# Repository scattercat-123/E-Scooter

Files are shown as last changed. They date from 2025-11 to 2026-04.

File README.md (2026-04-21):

# E-Scooter
## The powerfull electronic scooter with suspension and a 1 hour battery.

## Why its special:
 - has a powerfull motor using a chain link system better than wheel hub system found in mordern scooters.
 - A high capacity battery for extended uses
 - Digital system with throttle, brakes and Battery managment system
 - has a really good custom front wheel suspension.

## Why did I make this?
Hardware projects are fun to make and i wanted something more fun than walking while travelling from one place to another.

## How does it work?
this electric scooter works by using a 24v batte ry pack made from 18650 cells arranged in a 7s 4p configuration which provides the required voltage and enough current to run the scooter. the battery is managed by a bms which protects it from overcharge and overdischarge and balances the cells so the pack stays healthy and also lets it charge . power from the battery goes into the motor controller which regulates how much current flows to the my1020 500W motor depending on throttle input. the motor converts this electrical energy into rotational motion by drivingg the chain which spins the rear wheel and makes it move. the headset and frame hold everything aligned so the power transfer is efficient. the suspension is custom built with 2 cycle supensions attached on a 2 part linkage system, the suspension has enough clearance so that the scooter can easily travel over any bumps and terrain on the way.

## pics









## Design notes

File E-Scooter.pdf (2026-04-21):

# E-Scooter

## Assembly

Github: https://github.com/scattercat-123/E-Scooter

## Cut Mild Steel Sheets, Pipes & Tubes for Frame (x7)

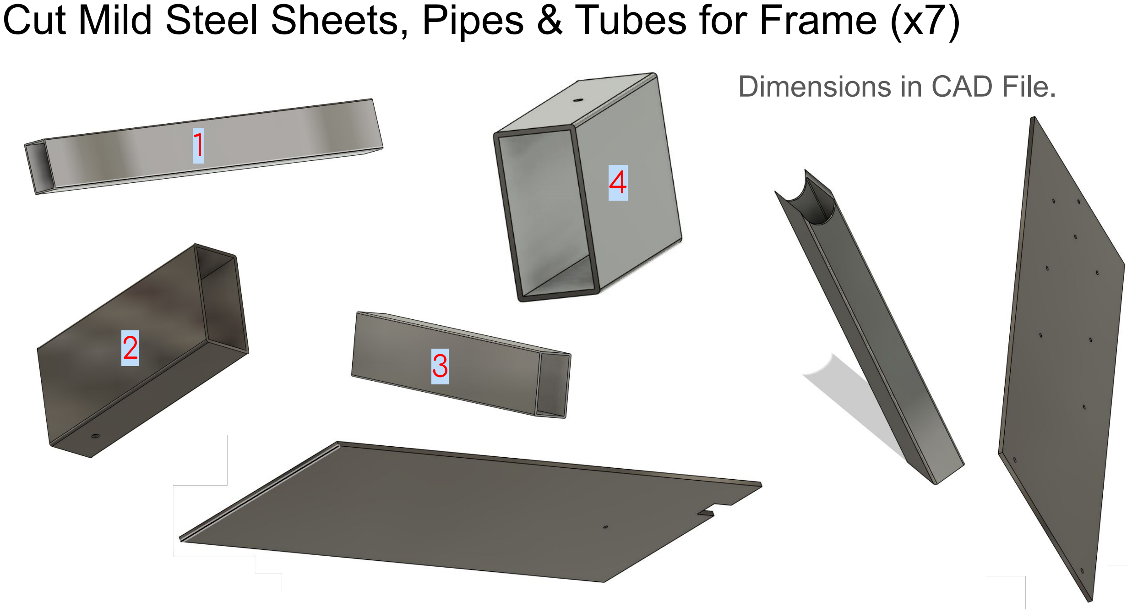
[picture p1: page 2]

Dimensions in CAD File.
1

2
3

4

## Step 1: Basic frame shape

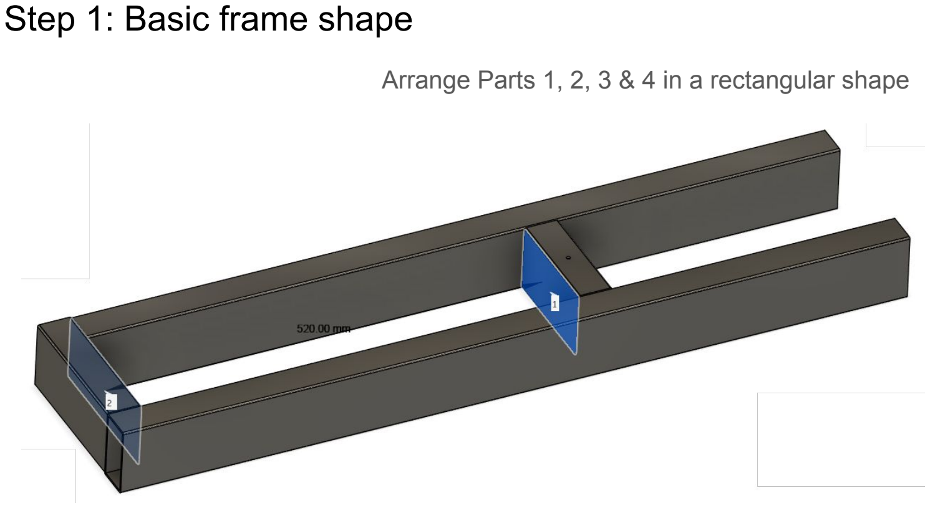
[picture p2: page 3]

Arrange Parts 1, 2, 3 & 4 in a rectangular shape

## Step 2: Basic frame shape

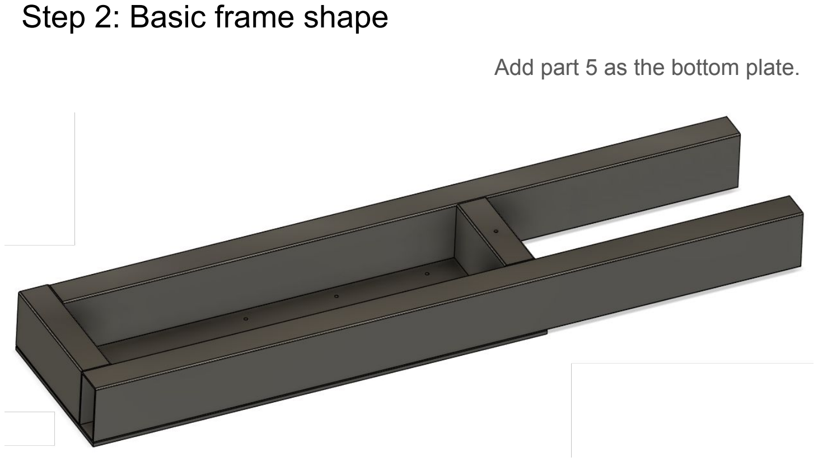
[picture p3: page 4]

Add part 5 as the bottom plate.

## Step 1: Electronics

Make the battery pack with 7S4P configuration by spot welding and adding spacers

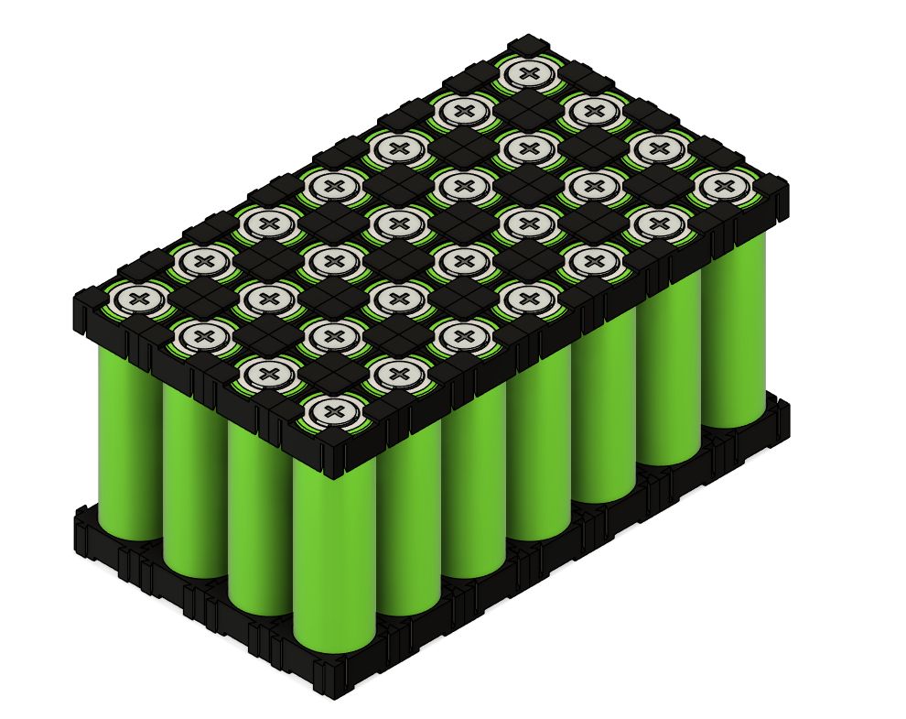
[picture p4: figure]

Watch this video to for an example about spot welding parallel and series cells for custom packs: https://www.youtube.com/watch?v=RuA0cUinqzA (https://www.youtube.com/watch?v=RuA0cUinqzA)

Note: Make sure to use 7S4P or even 5P configuration only!!

## Step 2: Electronics

Attach the BMS to the battery pack and wire according to the datasheet

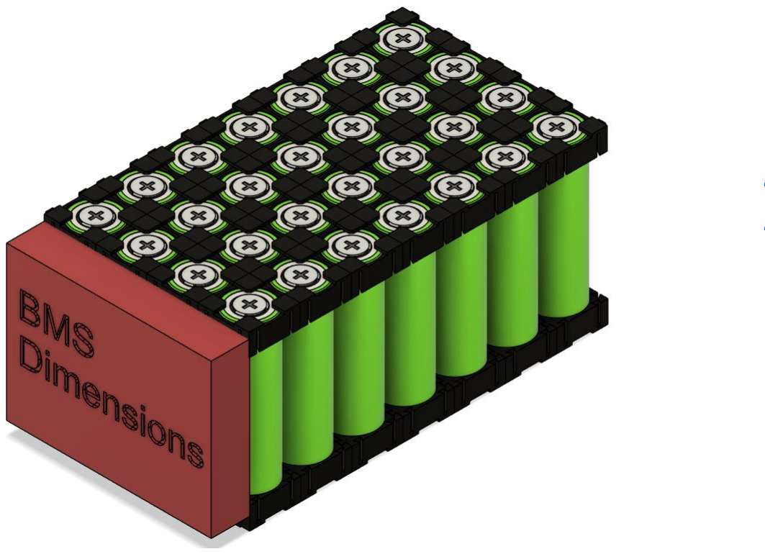
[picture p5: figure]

Here is a video by the bms manufacturer on how to wire the battery pack:
https://www.youtube.com/watch?v=KX7jc_Q_Cb8 (https://www.youtube.com/watch?v=KX7jc_Q_Cb8)

## Step 3: Basic frame shape

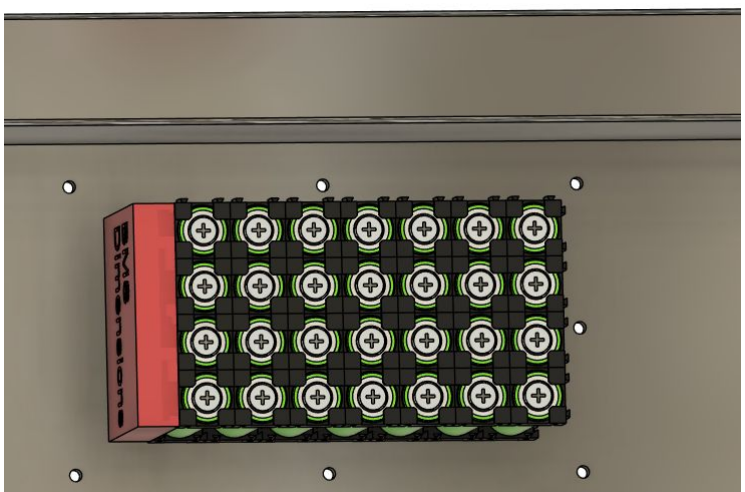
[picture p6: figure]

Place the battery inside the box made by the screw holes

## Step 4: Basic frame shape

Screw on the 3d printed battery cover and make sure no water/dust can enter

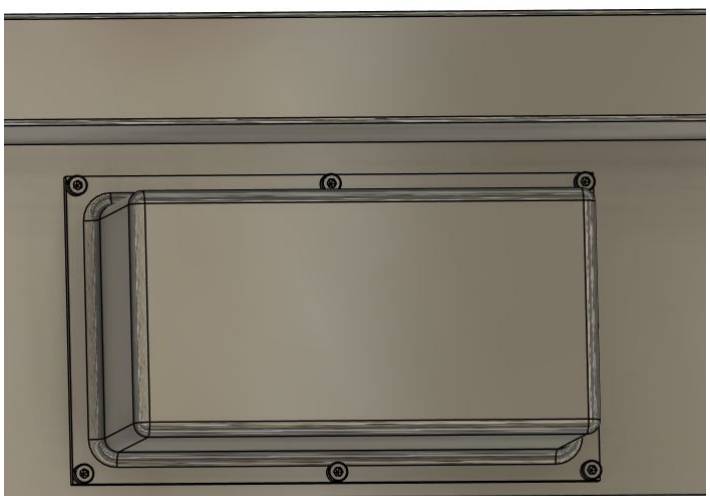
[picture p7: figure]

## Step 5: Basic frame shape

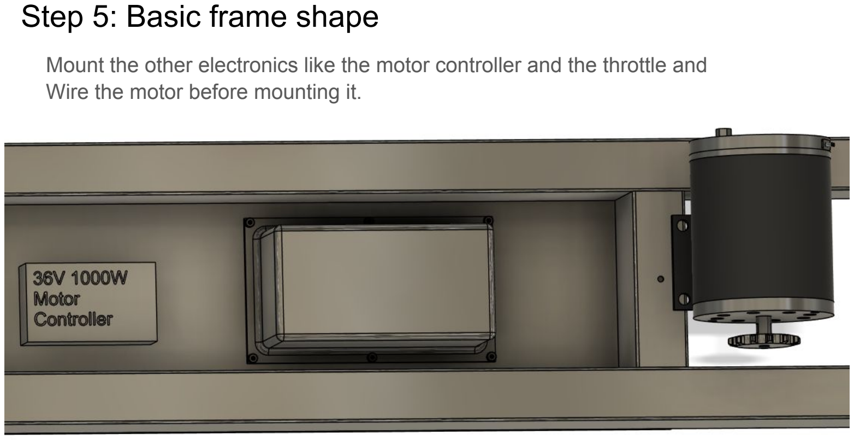
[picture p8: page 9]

Mount the other electronics like the motor controller and the throttle and Wire the motor before mounting it.

## Step 5: Basic frame shape

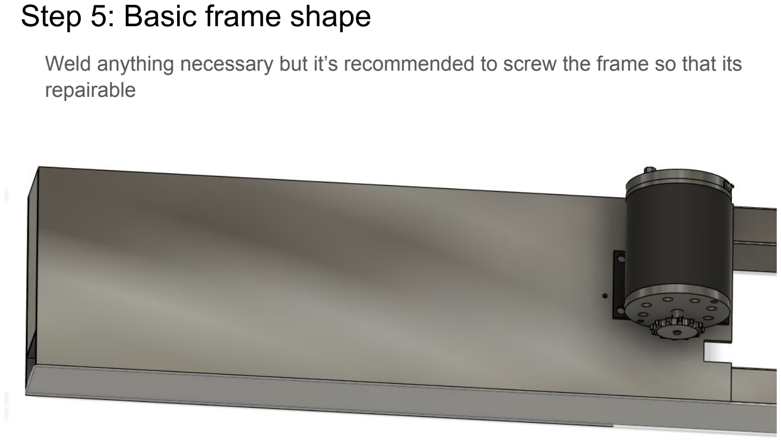
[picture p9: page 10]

Weld anything necessary but it’s recommended to screw the frame so that its repairable

## Step 1: Handlebars

Weld the handle support

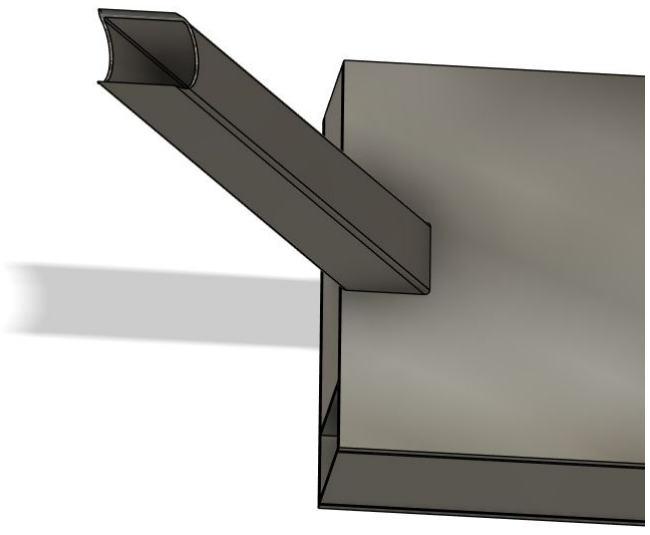
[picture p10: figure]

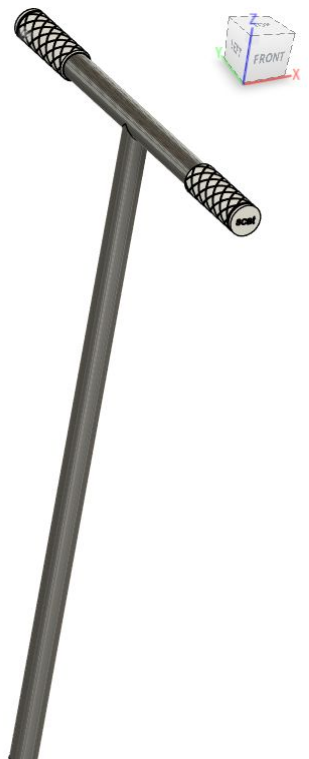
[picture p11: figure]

## Step 1: Handlebars

Make the T Handlebar shape

Obviously the white handlebars are just for a model but make sure to put the correct electronic ones with a throttle and perhaps a display?

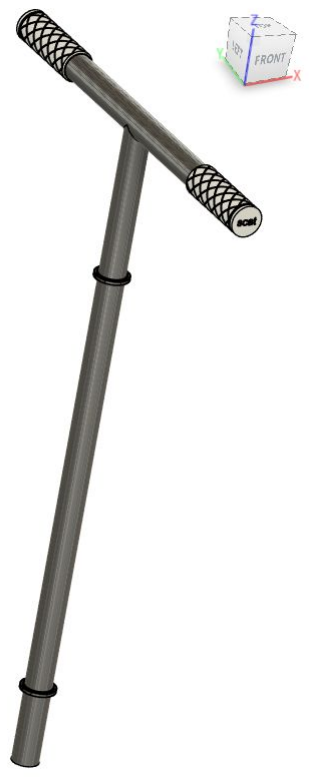
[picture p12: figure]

## Step 2: Handlebars

Attach the bearings

Just a breif idea but makes more sense in the cad design

## Step 3: Handlebars

Hammer the outer pipe which will be connected to the frame.

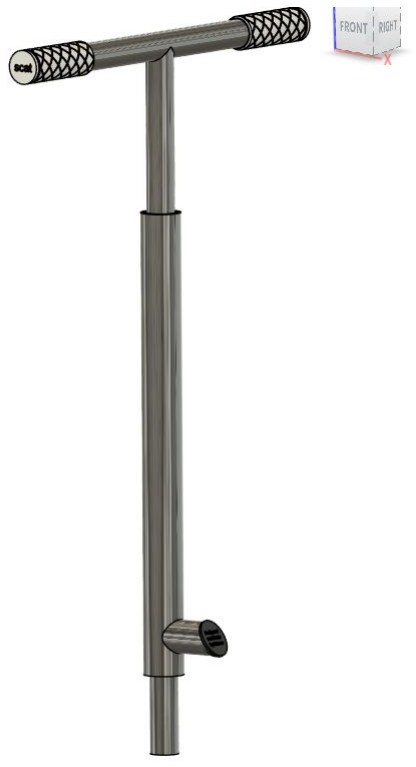
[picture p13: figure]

Just a breif idea but makes more sense in the cad design

## Step 4: Handlebars

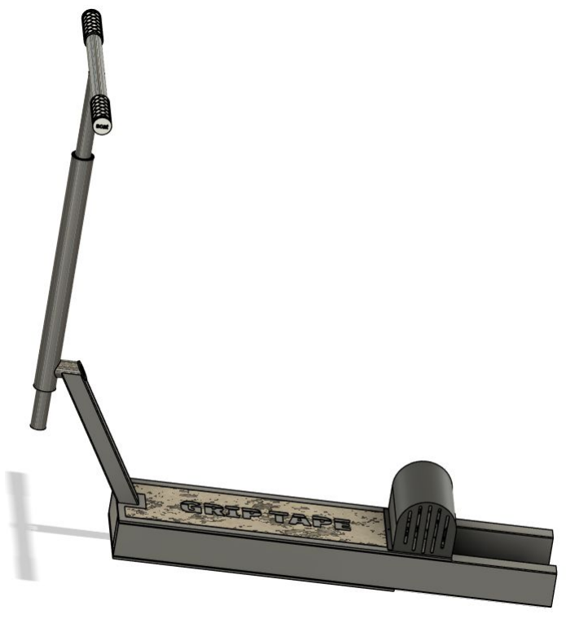
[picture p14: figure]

Attach it with the other part of the frame!

Now you have an almost done scooter! Remember to also cover the motor with the 3d printable cage so it doesnt cut your leg with the sprocket hehe.

## Step 1: Wheels

Assemble the rods and the 3d printed parts(petg)

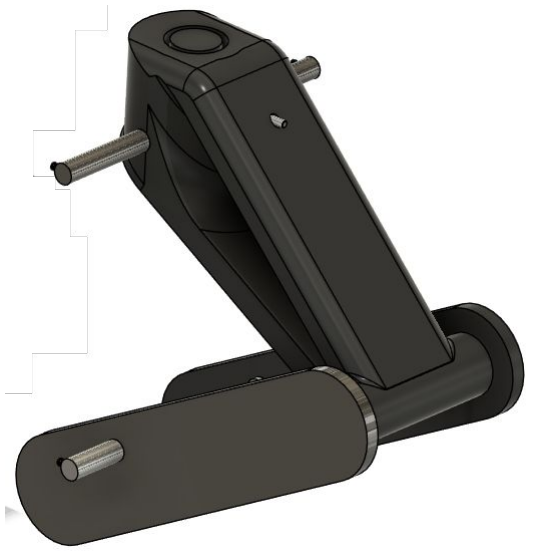
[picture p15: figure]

Both the parts have bearing in them so they can slide with each other for the suspension.

## Step 2: Wheels

Slide the suspension springs in the rods

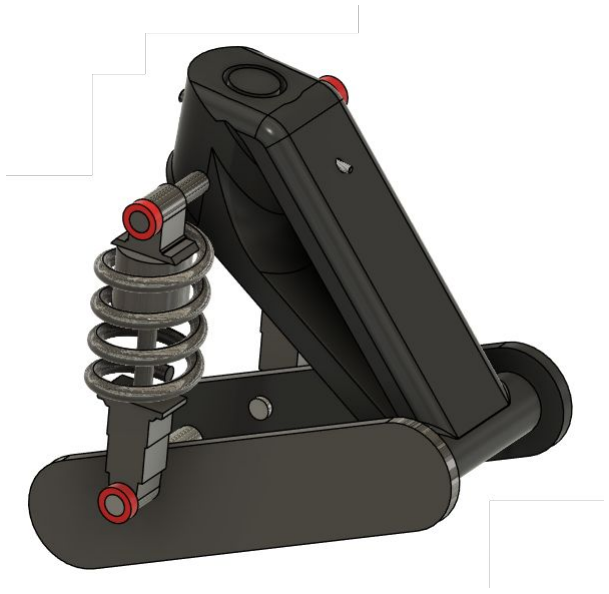
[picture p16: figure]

Carefully! Also attach the red 3D printable clips with brass inserts to prevent the suspension from sliding out the rods.

## Step 3: Wheels

Add the actual wheel!

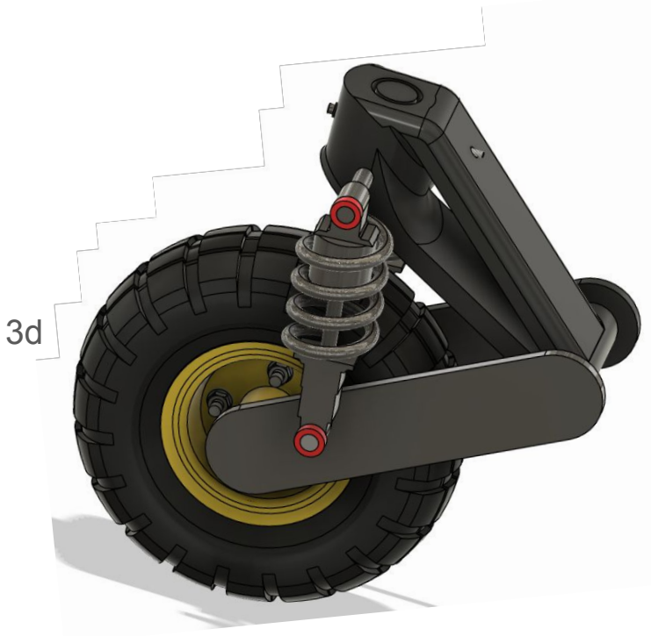
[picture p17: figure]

The wheel uses a rod to spin on the 3d printed parts.

## Step 4: Wheels

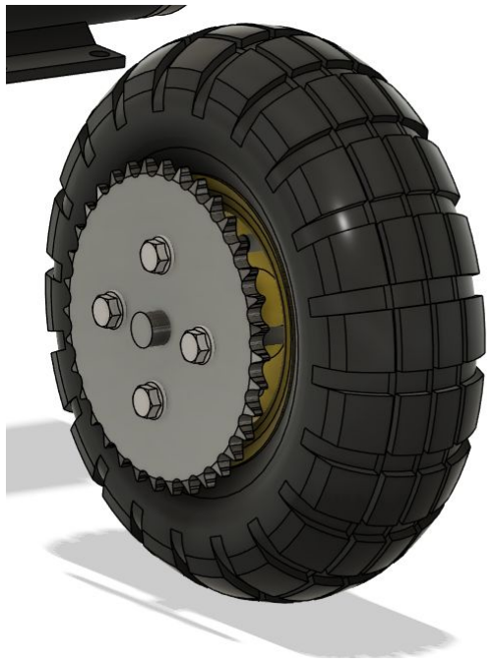
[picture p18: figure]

The back wheel

Use extra long screws and replace the old ones to attach the custom cnced sprocket. Remember to make a hole for the rod to be welded in the frame.

## Step 1: Final stuff

Attach everything together

Weld the back wheel’s axle to the

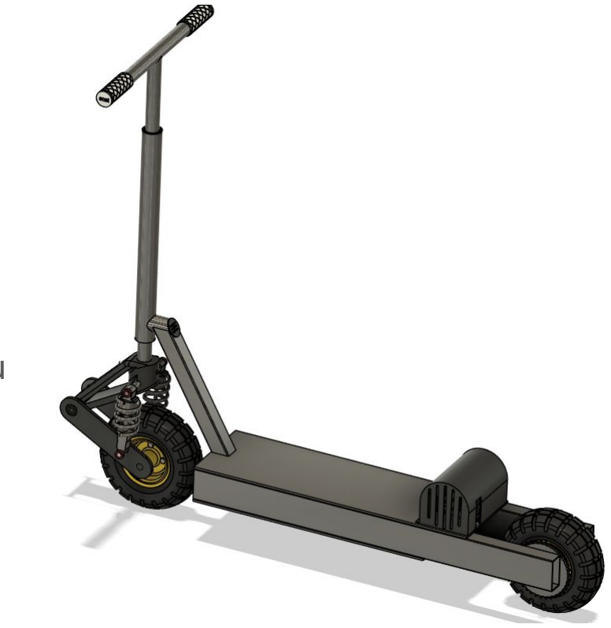
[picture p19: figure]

frame, attach the pipe in the hole of the front wheel 3d printed parts and you are all done!

## Step 2: Final stuff

It still wont work now!!

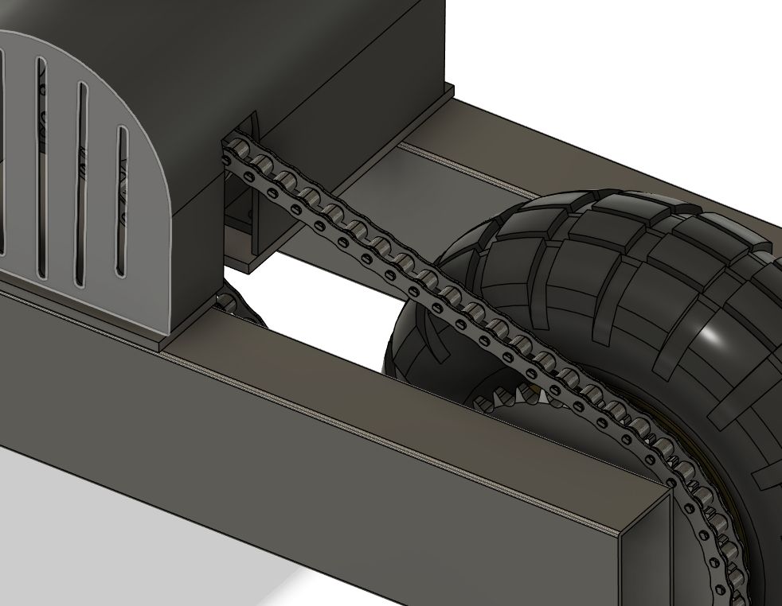
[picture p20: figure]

Attach the chain to the sprocket of the motor to the sprocket of the wheel

## Step 3: Final stuff

Aesthetics are important!

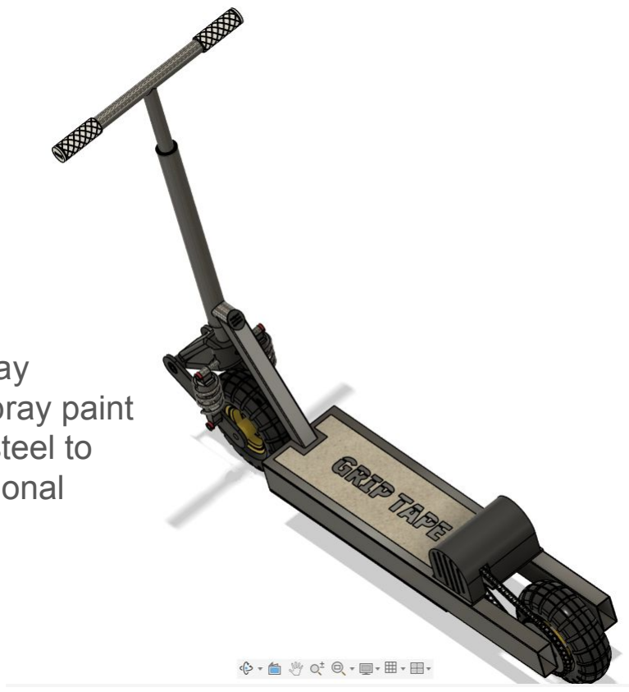
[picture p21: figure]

Stick grip tape with custom spray painted designs! And maybe spray paint the body if you are using Mild steel to prevent rust and add a professional look!

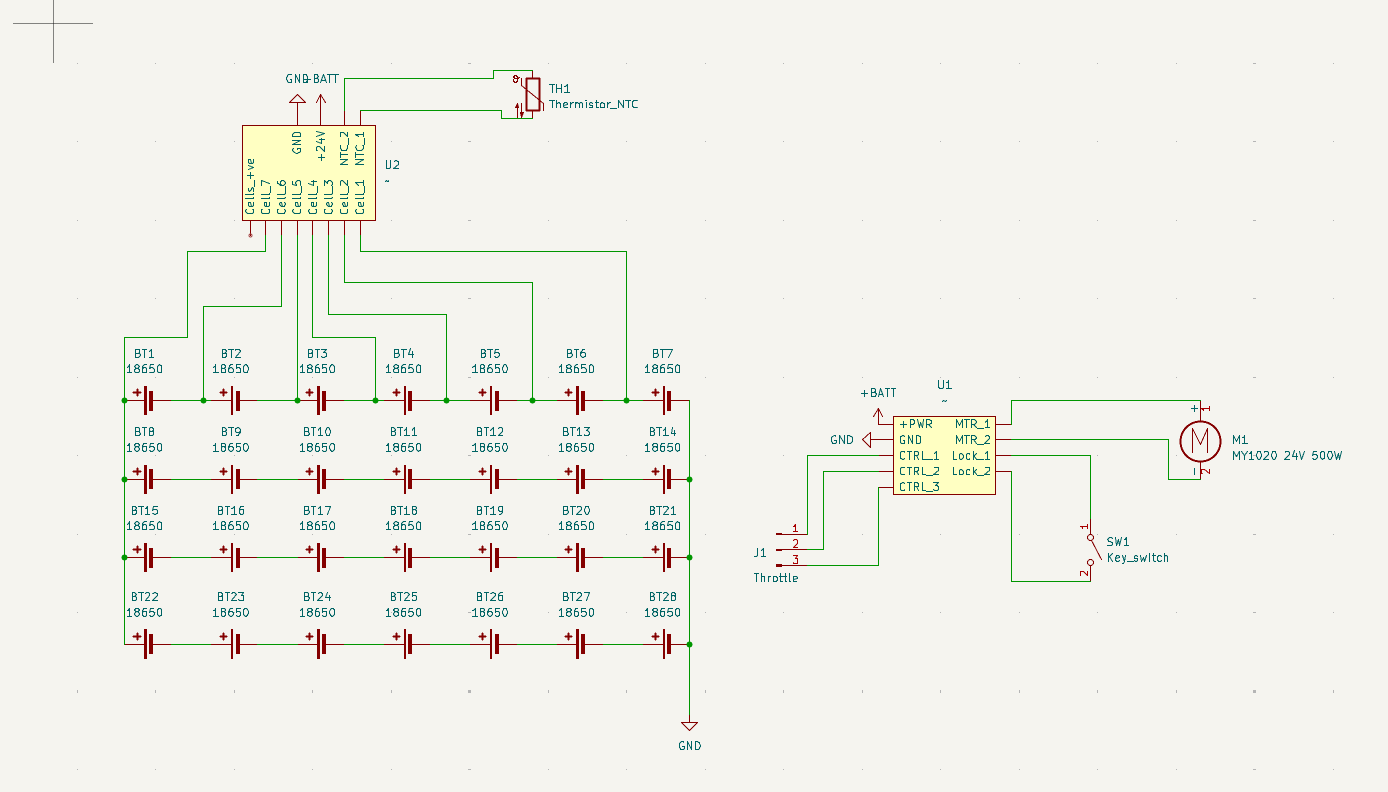
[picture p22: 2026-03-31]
Circuit diagram.png

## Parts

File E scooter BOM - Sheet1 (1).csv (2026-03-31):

No. | Name | Qty | Price in ₹ | Price in $ | Link | Notes
1 | MY1020 DC Brushless Motor | 1 | ₹5,293.00 | $56.53 | https://robu.in/product/500w-24v-dc-2500-rpm-for-scooter-bike-go-kart-minibike-e-atv-my1020/
2 | Custom sprocket for wheel T8F CNC | 1 | ₹5,617.59 | $60.00 | https://jlccnc.com/cnc-machining-quote
3 | Suspension for front wheel | 2 | ₹6,858.00 | $73.25 | https://www.alibaba.com/product-detail/DNM-DV-22AR-Bicycle-Suspension-Rear_1600563601893.html
4 | Spot welder for battery | 1 | ₹1,500.00 | $16.02 | https://roboticsdna.in/product/12v-battery-storage-spot-welding-machine-circuit-board/
5 | Throttle with voltmeter + key | 1 | ₹605.00 | $6.46 | https://robu.in/product/digital-throttle-with-key-for-ebike/
6 | BMS(battery managment system) 24V 7S | 1 | ₹1,511.00 | $16.14 | https://robu.in/product/daly-li-ion-7s-25-9v-40a-battery-management-system/#tab-robu_other_tab | Out of stock rn but new stock is coming :)
7 | Wheels (pneumatic) 10" | 2 | ₹3,598.00 | $38.43 | https://www.amazon.in/10-Inch-Pneumatic-Rubber-10x3-00-4-Bearing/dp/B0FKBJ31QK
8 | Grip tape for feet deck | 1 | ₹354.00 | $3.78 | https://www.amazon.in/Unity-Brand-Non-Slip-Traction-Slipping/dp/B0FPML39W1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
9 | 7S4P battery back 18650 cells | 28 | ₹10,976.00 | $117.23 | https://robu.in/product/lg-18650-mj1-3400mah-3c-li-ion-battery/ | Out of stock rn but robu team has informed that new stock is coming :)
10 | Motor controller 500W 24V | 1 | ₹881.00 | $9.41 | https://robu.in/product/motor-controller-24v-500w-my1020-diy-electric-bicycle-kit/
11 | MS steel and rods | 10 | ₹3,500.00 | $37.38 | Offline hardware store | For the frame.
12 | 12mm steel rod for suspension | 1 | ₹630.00 | $6.73 | https://www.amazon.in/VAKOOBA-Steel-12mm-diameter-lenght/dp/B0C56W8L2J
13 | 16mm steel rod for wheels | 1 | ₹450.00 | $4.81 | https://robokits.co.in/mechanical-parts/cnc-router-xyz-axis-part/astro-chrome-plated-steel-rods/astro-super-smooth-hard-chrome-plated-16mm-diameter-carbon-ste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
14 | #40 Roller Chain x 3 feet | 1 | ₹2,380.00 | $25.42 | https://www.amazon.in/PGN-Roller-Chain-feet-Connecting/dp/B07NPT53D4
15 | Screws+brass inserts | 10+ | ₹175.00 | $1.87 | https://onlyscrews.in/
16 | Bearings | 2 | ₹279.00 | $2.98 | https://www.bearinghouse.in/cart/
17
18
19
Total: |  |  | ₹44,607.59 | $476.44

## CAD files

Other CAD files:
E-Scooter.step

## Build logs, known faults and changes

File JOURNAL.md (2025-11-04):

<!--
  ===================    !!READ THIS NOTICE!!   ====================
  DO NOT edit this file manually. Your changes WILL BE OVERWRITTEN!
  This journal is auto generated and updated by Hack Club Blueprint.
  To edit this file, please edit your journal entries on Blueprint.
  ==================================================================
-->

## 11/3/2025 - Research and starting plans  

**Day 1:**
Today i researched various things such as the motor the chain and the overall build of the electric scooter, i already decided that i will se my1020 1000W 36v. Also, i modeled the motor in fusion and decided how i will be using the headset, the motor and battery pack made up of 18650 cells.



## 11/4/2025 - Started Modeling and research everything needed  

**Day 2:**

I modeled the battery:



Also i finalized which battery I would be using because yeah there ae many types of battery which give diffirent mah rating and discharge rate, i will be using 40 x LG INR18650MJ1 3400mAh (3c) LI-ION BATTERY
This is suitable because if i do 10S4P setup, it will give about 13 AH with 36 nominal voltage.

I also found the BMS module I will be using:


So this is my cheapest setup of the battery which is fully diy i would be spot welding
Today was like more of research

Helpfull video - [EBike Battery Pack || DIY](https://www.youtube.com/watch?v=b2sBhDxmPmA)

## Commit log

2026-03-31 Circuit diagram sch
2026-03-31 Added cad
    [E-Scooter.step]
2026-03-31 Updated cad
    [E-Scooter cad.step, E-Scooter.step]
2026-04-21 Added manual of how to build
    Its a bit breif but you must look through the cad to get more details.
2026-04-21 Add explanation of electric scooter functionality
    Added a section explaining how the electric scooter works, including details about the battery pack, motor controller, and suspension system.
2026-04-21 added updated cad
    [E-Scooter.step]
